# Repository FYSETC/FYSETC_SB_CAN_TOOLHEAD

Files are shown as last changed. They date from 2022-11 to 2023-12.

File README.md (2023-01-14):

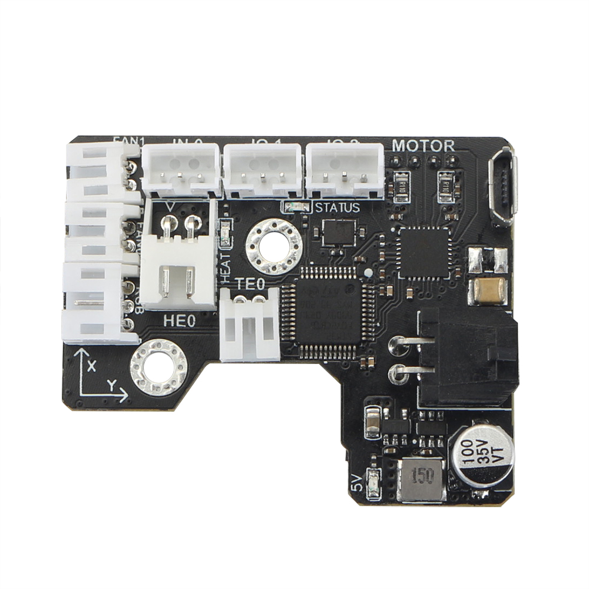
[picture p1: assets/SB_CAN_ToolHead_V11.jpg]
SB_CAN_ToolHead


# Introduction

The SB CAN Tool Board is a highly integrated printhead control board. Based on STM32F072, running Klipper firmware. Onboard TMC2209 stepper motor driver, AXL345 acceleration sensor, and other necessary interfaces. And comes with a 2.5m 4-core cable for easy out-of-the-box use.

# Feature

- Based on STM32F072
- Onboard 1M CAN transceiver
- Onboard TMC2209
- 2x 0.5A MAX PWM interface for controllable fan (default VIN power supply, 5V optional)
- 1x signal input interface (VIN power supply, with level conversion)
- 2x signal input and output interface (5V power supply, with pull-up resistor)
- 1X 5V single wire RGB interface (1A MAX)
- 1x 4A MAX PWM output for heating rod
- 1x ADC interface for heating rod temperature acquisition
- MX3.0 2X2 interface for power and CAN signal access
- 1x Micro USB for firmware uploading
- Comes with 2.5m 4-core cable, 2x16AWG+2x24AWG
- Comes with terminal housing and wire crimping tabs

# Where to Buy

Taobao

Aliexpress

Official website

# Docs

Check our wiki: [SB CAN TH - FYSETC WIKI](https://wiki.fysetc.com/SB%20CAN%20ToolHead/)

# Contact US

QQ group：1041794121

Facebook group：https://www.facebook.com/groups/197476557529090

Discord：https://discord.gg/Fb6FdND4

email：support@fysetc.com

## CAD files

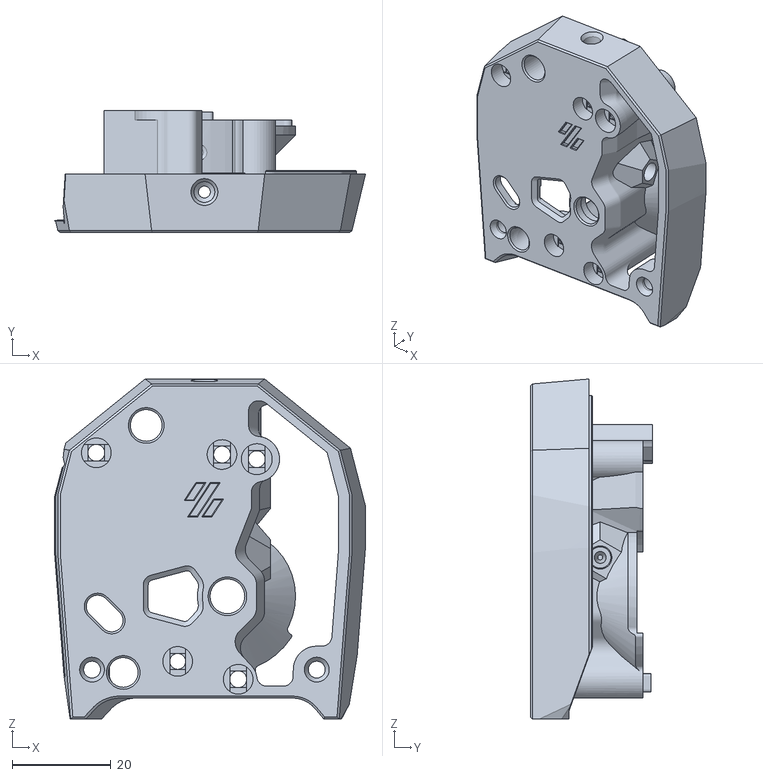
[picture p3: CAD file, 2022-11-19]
STLs/main_body^Clockwork2(2)_Clockwork2.STL
62.8 x 24.7 x 68.7

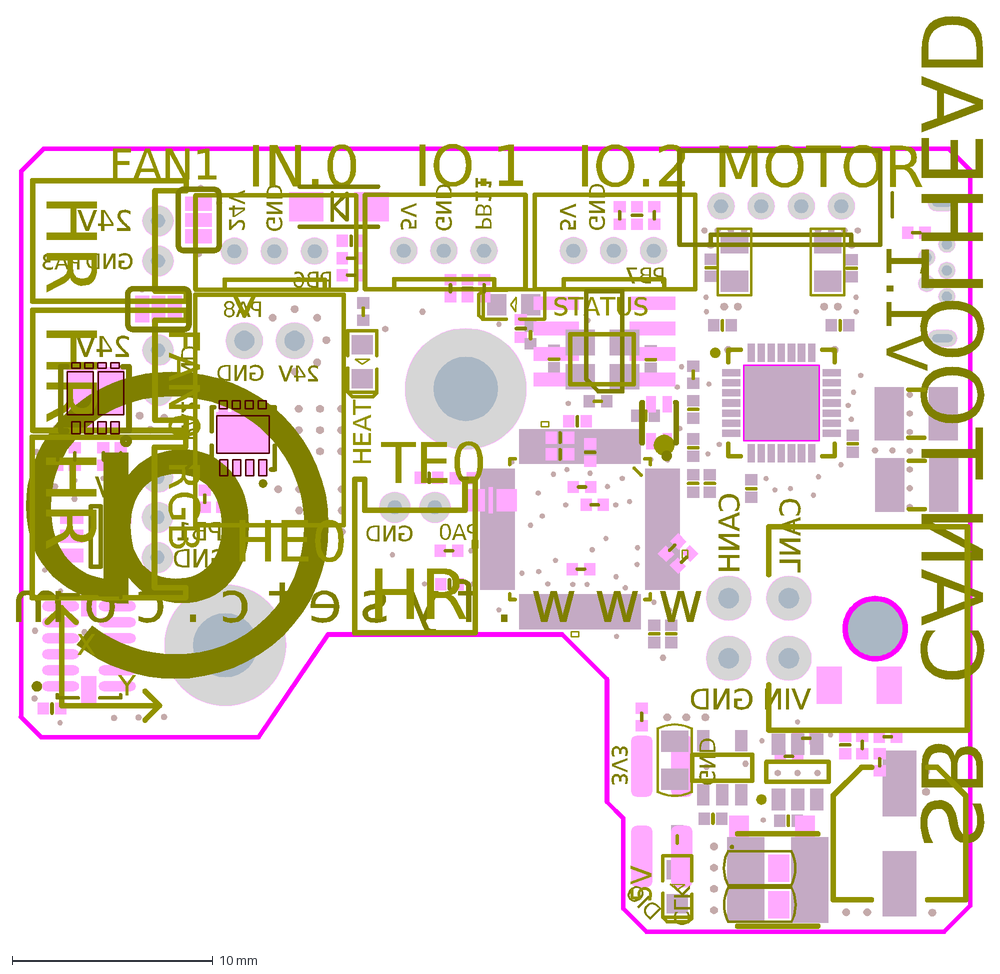
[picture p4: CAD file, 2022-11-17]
SB CAN TOOLHEAD V1.1.DXF
PA8
GND
V1.1
PB6
PA2
@
5V
24V
PB11
CANL
PB7
3V3
w w w . f y s e t c . c o m
PA3
PA0
PB1
CANH
DIO
VIN
SB CAN TOOLHEAD
CLK
IO.2
HE0
IN.0
FAN1
TE0
IO.1
FAN0
RGB
MOTOR
X
Y
STATUS
HEAT
HR

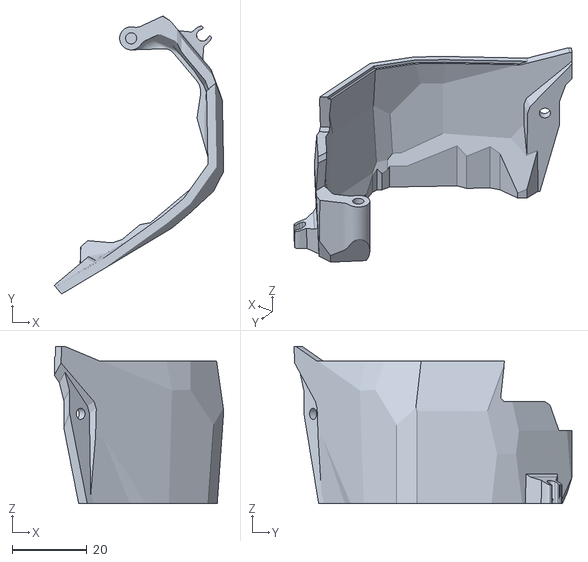
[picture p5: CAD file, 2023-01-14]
STLs/Clockwork2-adjusted.STL
45.4 x 74.5 x 42.2

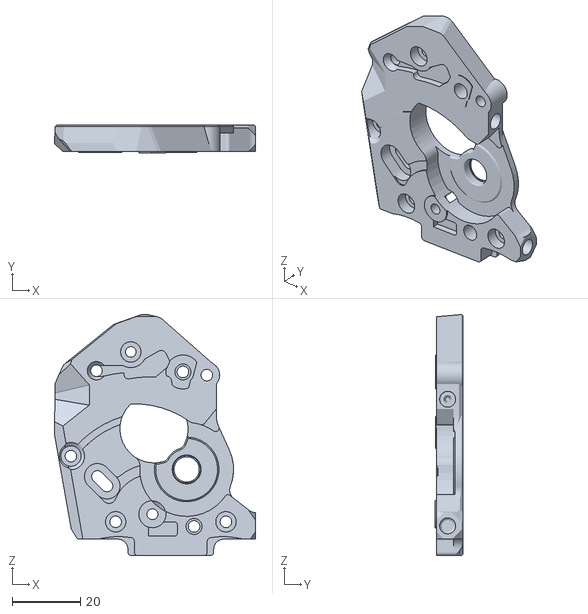
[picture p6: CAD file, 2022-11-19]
STLs/motor_plate^Clockwork2(2)_Clockwork2.STL
59.1 x 8.20 x 70.8

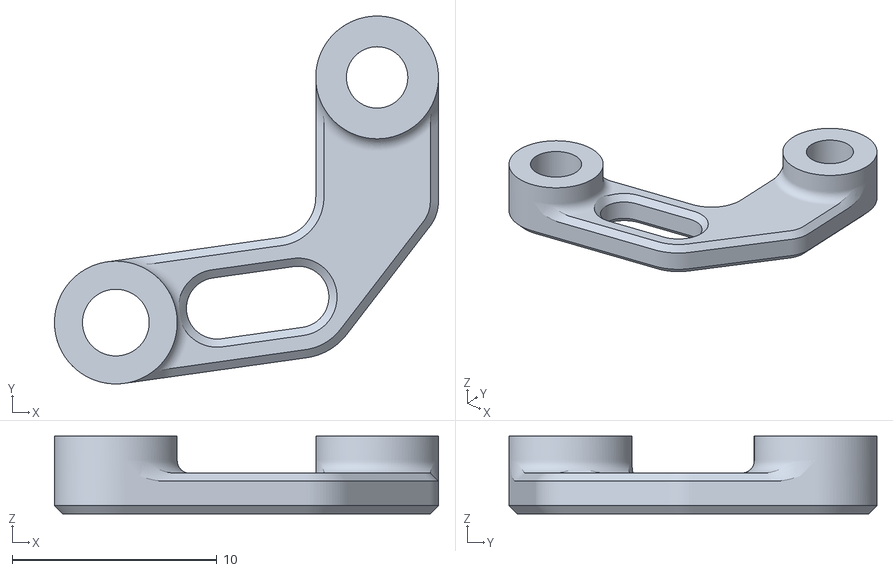
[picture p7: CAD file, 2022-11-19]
STLs/pcb_spacer.STL
18.8 x 18.0 x 3.80

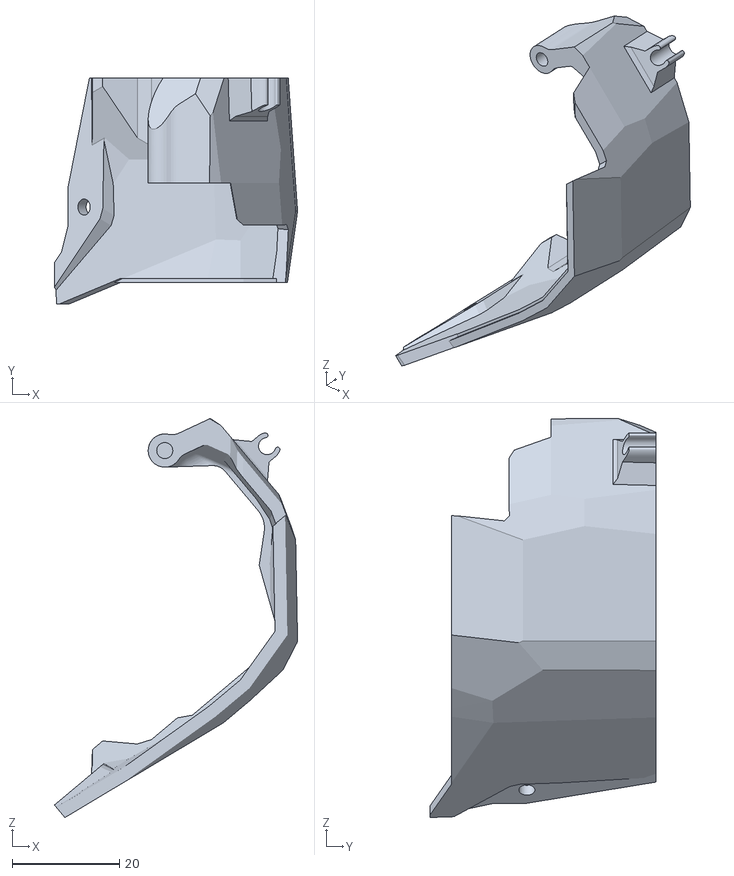
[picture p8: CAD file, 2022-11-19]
STLs/Clockwork2.STL
45.4 x 42.2 x 74.5

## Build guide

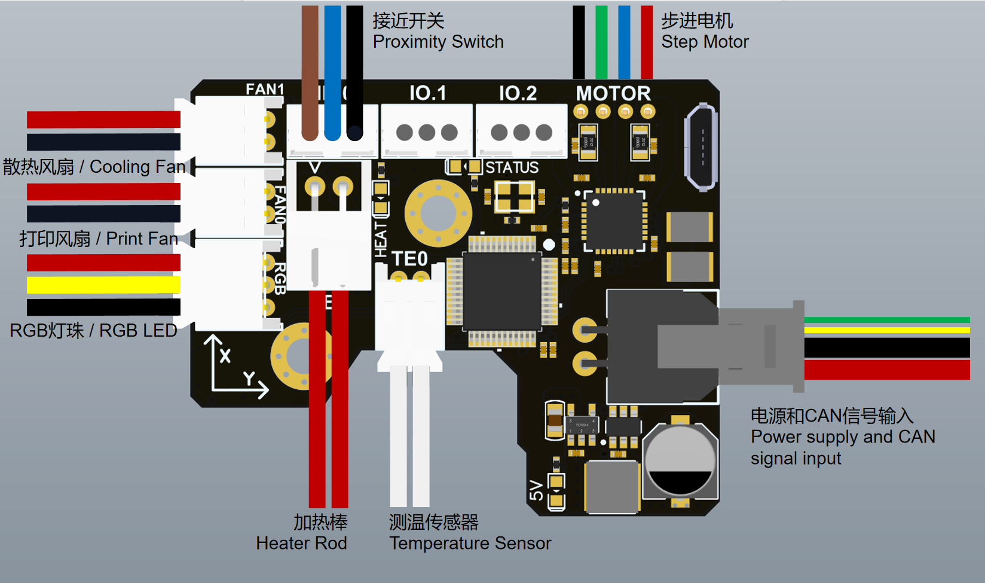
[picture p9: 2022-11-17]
assets/SB CAN ToolHead_Wiring.png

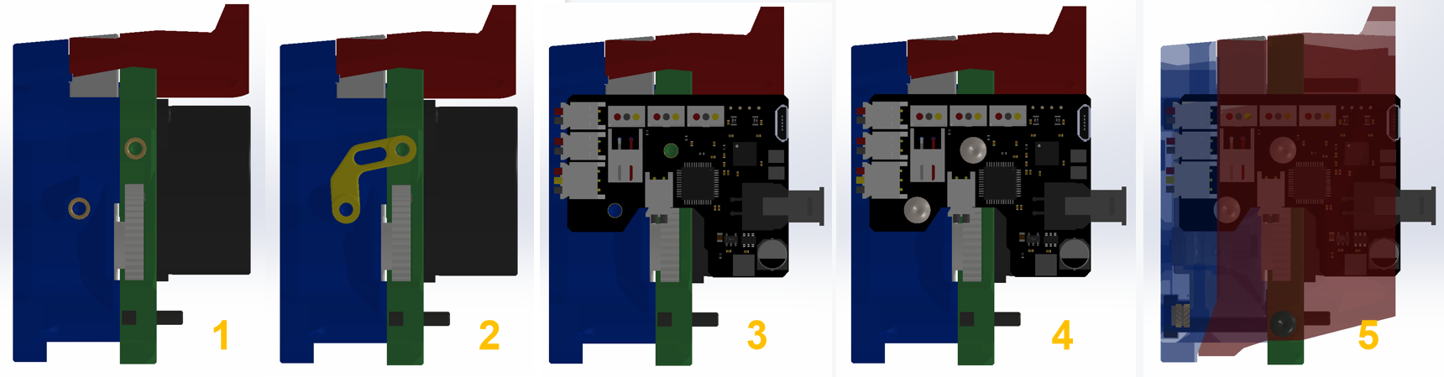
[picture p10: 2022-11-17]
assets/SB CAN ToolHead_Install.png

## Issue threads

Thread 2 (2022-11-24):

蜘蛛主板can收发器,配合sb_can_toolhead的使用方法

git-czy, 2022-11-24:
menuconfig：
蜘蛛主板menuconfig
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
sb_can_toolhead menuconfig
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
问题：
1.使用`~/klippy-env/bin/python ~/klipper/scripts/canbus_query.py can0`命令只能查询到主板的uuid,无法获取sb_can_toolhead的uuid。已经困扰几天了
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
取下收发器也只有一个uuid，是因为收发器没有正常工作？
2.wiki上的https://wiki.fysetc.com/SB%20CAN%20ToolHead/，menuconfig配置的STM32F103，sb_can_toolhead使用的STM32F072芯片，是不是不太对

求蜘蛛主板can收发器,配合sb_can_toolhead的正确配置方法

git-czy, 2022-11-24:
正确的配置方法，蜘蛛主板menucofnig见问题中图，sb_can_toolhead menuconfig如下图
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

最终效果如下
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
有两个uuid,取下can板再执行一次命令，即主板uuid

GerogeFu, 2022-12-03:
蜘蛛主板如果不需要加入到 CAN BUS 网络中，就采用 USB 或者 串口的配置进行连接即可，如果用 CAN 收发器的将蜘蛛主板加入到 CANBUS 网络的话，按以下配置
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
你可以先不管蜘蛛主板的，先把 SBCAN 的 CAN 调通，然后再来调试蜘蛛板的 CAN

git-czy, 2022-12-03:
> 蜘蛛主板如果不需要加入到 CAN BUS 网络中，就采用 USB 或者 串口的配置进行连接即可，如果用 CAN 收发器的将蜘蛛主板加入到 CANBUS 网络的话，按以下配置 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 你可以先不管蜘蛛主板的，先把 SBCAN 的 CAN 调通，然后再来调试蜘蛛板的 CAN
>
> SBCAN 正确的接线应该是 树莓派 -> UCAN模块 -> CANBUS -> SBCAN 模块

谢谢，我按照这种方法，已经解决了，目前正常使用

Closed 2022-12-03.

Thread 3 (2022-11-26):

Differences between STLs in this repository and the official stealthburner repo

geoffdavis, 2022-11-26:
Other than the "hook" on the top of `Clockwork2.STL`, I can't find any differences in the shape of the objects in this repository and the office Voron STLs.

Am I missing something, or is it just a matter of old STLs from the beta version of the Stealthburner?

23Jacky, 2022-12-13:
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
Cutting is done here

numindast, 2023-01-09:
It would be good to know if the "main body" and "motor plate" STLs are any different from the Stealthburner stock parts.

I'm also curious as I would like to print an ERCF main body myself to get the ECAS fitting on top, but want the SB CAN PCB to work as intended too. Thanks!

Interfredzo, 2023-11-29:
I've noticed that most changes are due to old beta data used.
Also the board colides with the spacer (the official and the one provided by fysetc).
I've compared the original release date of the motorplate from the voron team (green transolcent) with the one from fysetc. The diferences are not realted to the PCB at all. ->Use the official voron repo data and mirror the space
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
r.
![collisionSpacer](https://github.com/FYSETC/FYSETC_SB_C
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
AN_TOOLHEAD/assets/123958845/8ac8dbe7-e5ee-48a0-acaf-e47c895c8559)

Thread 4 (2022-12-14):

Does this toolhead PCB require the CAN bus expander?

OzzieOrca, 2022-12-14:
I've got a Spider V1.1 board and am looking at purchasing this toolhead PCB from https://www.fysetc.com/products/fysetc-sb-can-tool-board-based-on-stm32f072-support-klipper-with-tmc2209-axl345-acceleration-sensor-for-3d-printer-parts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.

Is this CAN bus expander required?
https://www.fysetc.com/products/fysetc-canbus-expander-module-for-spider-board?variant=42187841994927

In this repo/wiki you've got a bunch of pinouts for the toolhead PCB but not how to connect it to the Spider. https://github.com/FYSETC/FYSETC-SPIDER#can-bus shows using it but for connecting to the Raspberry Pi. I assume it's needed to go from UART to CAN bus? Does the CAN bus expander GND need to be tied to ground?

I'm going to be using the Stealthburner Rapido toolhead and probably leave the Clockwork 1 in place. Looks like the Clockwork 1 might be missing a mounting screw hole? I'll figure something out.

Anything else I should know as far as compatibility? Will I be ok with the V1.1 Spider board?

Either way, updating the docs to mention whether it's required and how to connect would be great :) I could make a PR if needed.

Thanks!

numindast, 2023-01-09:
The Spider CAN expander is not required, unless your intention is to operate the Spider via CAN from the Klipper host. My understanding is this is not necessary and not always desirable.

I've got the expander also and it's just going to sit in a box. In my case, I use UART from the Raspberry Pi to the Spider (rather than USB, but either is perfectly acceptable). Add the UCAN to a USB port on your Pi and the other end of the UCAN is the CAN bus to the toolhead. Just wired this up today and it works.

Hope this helps

MdShahrilOGP, 2023-04-09:
Hello @numindast, I sincerely apologise for tagging you directly, but I am attempting to set up the SB CAN TH but am failing rather miserably. I am on a spider v2.2, and the connection goes like this RPI > UCAN > SB CAN TH. I followed the FYSETC's guide [here](https://wiki.fysetc.com/SB%20CAN%20ToolHead/) but I still can't get hte canbus_uuid at all. I've inserted the can0 config into /etc/network/interfaces.d directory too, but nothing works.

May I please ask the steps you took to get yours working? Thanks in advance sir!

numindast, 2023-04-10:
Hi - what are you seeing when trying to run the `canbus_query.py` script? Nothing at all (eg. returns to shell prompt) or a bunch of errors?

Here's the process I followed. I'm probably overexplaining but hopefully if you missed a step you can catch it, or else this could be useful for someone else.

First connecting USB to the RPi from the UCAN. You should be able to `lsusb` and be able to see the following USB device in the output:
`Bus 001 Device 003: ID 1d50:606f OpenMoko, Inc. Geschwister Schneider CAN adapter`

If not, try a different USB cable perhaps, or a different USB port on the RPi. The UCAN came out of the box with the "candleLight" firmware so I did not have to flash the UCAN firmware myself. You won't be able to make progress until that entry is shown above in your `lsusb`.

You can confirm if your RPi likes the can0 setup by checking with `ifconfig` and view the output:

`can0: flags=193<UP,**RUNNING**,NOARP>  mtu 16
        unspec 00-00-00-00-00-00-00-00-00-00-00-00-00-00-00-00  txqueuelen 128  (UNSPEC)
        RX packets 14816  bytes 111412 (108.8 KiB)
        RX errors 0  dropped 0  overruns 0  frame 0
        TX packets 1164  bytes 6843 (6.6 KiB)
        TX errors 0  dropped 0 overruns 0  carrier 0  collisions 0`

"Running" is what you want to see here. If it's not running, try `sudo ip link set can0 up type can bitrate 500000` (shamelessly stolen from the Voron discord #voron_electronics pinned posts). If that fails, ask in Discord for help, because I don't know.

Next up, connect your toolhead cable (you don't even need to install the PCB to start talking to it). The 4-pin Molex goes on the PCB of course, and the other end - CAN H/L to the appropriate screw terminals, and GND to a V- on your 24v power supply. That's also going to be where the CAN cable's power wires go, V+ and V- as well. You may already have done this, just confirming though. GND or V- need to be connected from both UCAN and the CAN cable to the toolhead.

Also, the 24v power must be turned on to power the toolhead PCB, it will not light up from just the CAN H/L wires. You'll know it's powered up when a red LED goes on near the bottom of the board.

If you haven't yet, here is when you can flash Klipper to the toolhead's MCU. Link to [Fysetc's Wiki on that here](https://wiki.fysetc.com/SB%20CAN%20ToolHead/#3-firmware-guide).

Be sure to follow their steps carefully. It's worth the extra effort.

The [RPi should be able to see/report](https://www.klipper3d.org/CANBUS.html#finding-the-canbus_uuid-for-new-micro-controllers) an uninitialized STM32 on the bus. Snag that canbus_uuid, stick it in your printer.cfg (I named mine `[mcu toolhead]`) and go forth.

Good luck - report back!

Kravenovic, 2023-04-10:
Hello @numindast, thank you so much for taking the time to reply me! Running this command `~/klippy-env/bin/python ~/klipper/scripts/canbus_query.py can0` returns this output:

```
Traceback (most recent call last):
  File "/home/pi/klipper/scripts/canbus_query.py", line 64, in <module>
    main()
  File "/home/pi/klipper/scripts/canbus_query.py", line 61, in main
    query_unassigned(canbus_iface)
  File "/home/pi/klipper/scripts/canbus_query.py", line 21, in query_unassigned
    bustype='socketcan')
  File "/home/pi/klippy-env/lib/python3.7/site-packages/can/interface.py", line 127, in __new__
    return cls(channel, *args, **kwargs)
  File "/home/pi/klippy-env/lib/python3.7/site-packages/can/interfaces/socketcan/socketcan.py", line 594, in __init__
    bind_socket(self.socket, channel)
  File "/home/pi/klippy-env/lib/python3.7/site-packages/can/interfaces/socketcan/socketcan.py", line 459, in bind_socket
    sock.bind((channel,))
OSError: [Errno 19] No such device
```

When I use `lsusb` I get this:

```
pi@mainsailos:~/klipper $ lsusb
Bus 002 Device 001: ID 1d6b:0003 Linux Foundation 3.0 root hub
Bus 001 Device 005: ID 1d50:614e OpenMoko, Inc.
Bus 001 Device 002: ID 2109:3431 VIA Labs, Inc. Hub
Bus 001 Device 001: ID 1d6b:0002 Linux Foundation 2.0 root hub
```

I don't see the `OpenMoko, Inc. Geschwister Schneider CAN adapter`.
Based on all the information I received from you, it seems that the problem lies with the fact that I still do not have a can0 interface which is up; despite me configuring the can0 file in /etc/network/interfaces.d

Once again, thank you so much for replying and for the assistance! Hope I can get this working soon!

numindast, 2023-04-10:
Hello - the OpenMoko is probably the UCAN. Unplug it and do another `lsusb` to see if that entry disappears. I'm not sure what it means that the OpenMoko USB descriptor in the output is different. I had the bad fortune not to have any issues so I'm not in a position to have a good idea.
If you aren't already on the Voron discord, definitely ask there in the #voron_electronics sub. There are a lot of people there with more experience (and brains!) than me!

I can think of one question: what OS are you operating on your RPi? Is it Raspberry Pi OS? Debian Buster or Debian Bullseye (newer)? I wonder if your Pi really is ready for can0. I don't recall installing anything but I'm using a new Bullseye install from the Pi foundation, and used Kiauh to set up all the "stuff" for me for Klipper (etc).

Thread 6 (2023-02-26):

Will this board handle a Rapido hotend?

RZ3D, 2023-02-26:
Will this board handle a Rapido hotend or is the draw too high?

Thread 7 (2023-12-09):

FYSETC Vorn SB CAN Toolhead V1.3

solrac8874, 2023-12-09:
Where can I find installation, schematics, etc. V1.3 version of this tool head?  I tried installing it using the Fystec SB CAN Toolhead Wiki (https://wiki.fysetc.com/SB%20CAN%20ToolHead/#31-menuconfig).  But when following trying to do 3.2 Firmware Upload step 4: Plug in SB-CAN-TH board 24v socket to power on it( Get the power from machine PSU); the Vin Fuse popped.  Now the board no longer powers on.

The wiki page and github site for the Fystec SB CAN Tool Head is only for V1.1 of the board and have not be updated for V1.3.  Seems like my board was fried from following the V1.1 Wiki Instructions.

Interfredzo, 2023-12-11:
Can confirm this!!!!!

Following all steps destroys the board after flashing!!!

eliwong, 2023-12-13:
We already updated the wiki. Please check!

solrac8874, 2023-12-13:
Thanks. I wish the wiki and github were updated several months ago before I bought the CAN Toolhead board in September 2023 or when V1.3 was released.

The wiki & github should have or include pictures of the V1.3 board front & back.  Also maybe helpful to highlight the differences between V1.1 & V1.3 board (e.g. different specs, components, etc.) like the Amazon product page describes.

Is the Vin Fuse (F1 - 5A) part shown on the V1.3 schematic/position diagrams the same as the Vin Fuse (F1 - ASMD1206-300) part shown on the V1.1 schematic/position diagrams?  The V1.3 schematic doesn't show the fuse part number like the V1.1 schematic. Are there any other components besides the fuse that are different and potentially at risk of being damaged by following the original V1.1 instructions?

I'm hoping I can just replace the Vin Fuse and get the V1.3 board working again so I can try to follow the new V1.3 instructions and confirm the new updates work.

Interfredzo, 2023-12-13:
The TMC2209 might be damaged.

I've also noticed that JP3 and R18 are actually missing on the board:

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

solrac8874, 2023-12-15:
R18 and JP3 are missing from my board too...  hope that's not a mistake.  Seems R18 and JP3 trace to CANL and CANH.
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

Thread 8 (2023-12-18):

CAN 120 Ohm terminating resistor missing on V1.3

Interfredzo, 2023-12-18:
The 120 ohm terminating resistor is missing on the actual PCB.

See JP3 and R18 on the shematics.

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

Also seems to be the case in the official product shots:

[https://ae01.alicdn.com/kf/S26268b260ddb4098bd3d542a5e0a9499Z.jpg](url)

Gagag1998, 2023-12-19:
Hello, dear friend, it seems that your motherboard is version V1.1, which is not available in this version. It is only available in version V1.3.
https://www.aliexpress.us/item/3256804693763411.html?

thisiscam, 2024-01-14:
I can verify this on my board. The CANH and CANL are completely disconnected with no termination resistors in between. This board doesn't seem to function correctly either --- I get consistent MCU timeouts on this board.

Interfredzo, 2024-01-29:
This is also the case on v1.3b. Soldering pads are present now compared to V1.3 but the resistor is missing. (Labeling for both boards is v1.3 though). I got a replacement board from FYSETC after the fuse and tmc driver blew up because i followed the manual ...

I soldered a 120ohm 0805 resistor to R18 now it's working.

To bad FYSETC is sending out boards which couldn't function in first place (resitors missing or not even planed). Or which blow up because the docu is not updated.

At least the customer support was fast in sending a replacement. And the wiki is updated now.
Would be nice if FYSETC will update their wiki so that everyone knows there needs to be a 120R if you use this as CAN end node (which is the default case for most users)

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

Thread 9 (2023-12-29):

Fan tachometer?

thisiscam, 2023-12-29:
Is the "fan0 tach" pin in the schematics actually connected to anything?

Interfredzo, 2024-01-29:
No. I also have a tach for the hotend. which I would highly recommend: https://ellis3dp.com/Print-Tuning-Guide/articles/useful_macros/hotend_fan_monitoring.html Had one fan failing and luckily I was near by.

You could use one of the IO connectors I guess. I will try it and leave a comment.

thisiscam, 2024-01-29:
I'm confused. If it's not connected to anything, how do you plan to use that pin? Are you suggesting soldering a wire onto the STM chip leg?

Interfredzo, 2024-01-29:
You can try soldering directly to the STM chip leg. I wouldn't recommend this unless your SMD soldering skills are very good. I would suggest using PB.6 PB.11 or PB.7 wich are on IN.O, IO.1 and , IO.2.. The tach signal connects the pull up to ground so the supply voltage of the van schould be irrelevant. So just connecting the ground and power of the fan to fan.0 or fan.1 and connecting the tachometer pin from the fan to the signal pin of IN.O, IO.1 and , IO.2 should work.

I guess the config should look like this. For Fan1 and signal to BP11 on IO.1
```
[fan_generic sb_can_fan1]
pin: sb_can_th:PA3
tachometer_pin: sb_can_th:^PB11
```

I didn't tried it yet and im no electronics engineer ;-) So no 100% guarantee.

Interfredzo, 2024-02-12:
OK I tested it with a Sunon 5V MF40100V1-1000U-G99 connected to IO.2: Power to 5V and Singal to PB7 to FAN1 only fround to PA.3

```
[fan_generic testfan]
pin: sb_can_th:PA3
tachometer_pin: sb_can_th:PB7
max_power: 1
cycle_time: 0.1
shutdown_speed: 0.0
kick_start_time: 0.5
off_below: 0.20
```
Since PB7 has a 10k pull-up already I didnt change it. Works flawless.

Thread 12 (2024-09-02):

Connector type for the power/CAN input on v1.3?

seanauff, 2024-09-02:
Does anyone know what connector this is? I would like to create a cable but can't find this connector anywhere

seanauff, 2024-09-03:
I managed to find it! It is an XT30(2+2). See [here](https://www.wellnowus.com/xt30pw22-male-gold-plated-plug-with-signal-pin-product/). Many options available on Aliexpress

Closed 2024-09-03.

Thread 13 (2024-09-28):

Step file of v1.3 corrupted?

5teveO, 2024-09-28:
I have downloaded the step file multiple times and opened in several different CAD packages.. none will open the file.

Are you able to replace the file with a working version?

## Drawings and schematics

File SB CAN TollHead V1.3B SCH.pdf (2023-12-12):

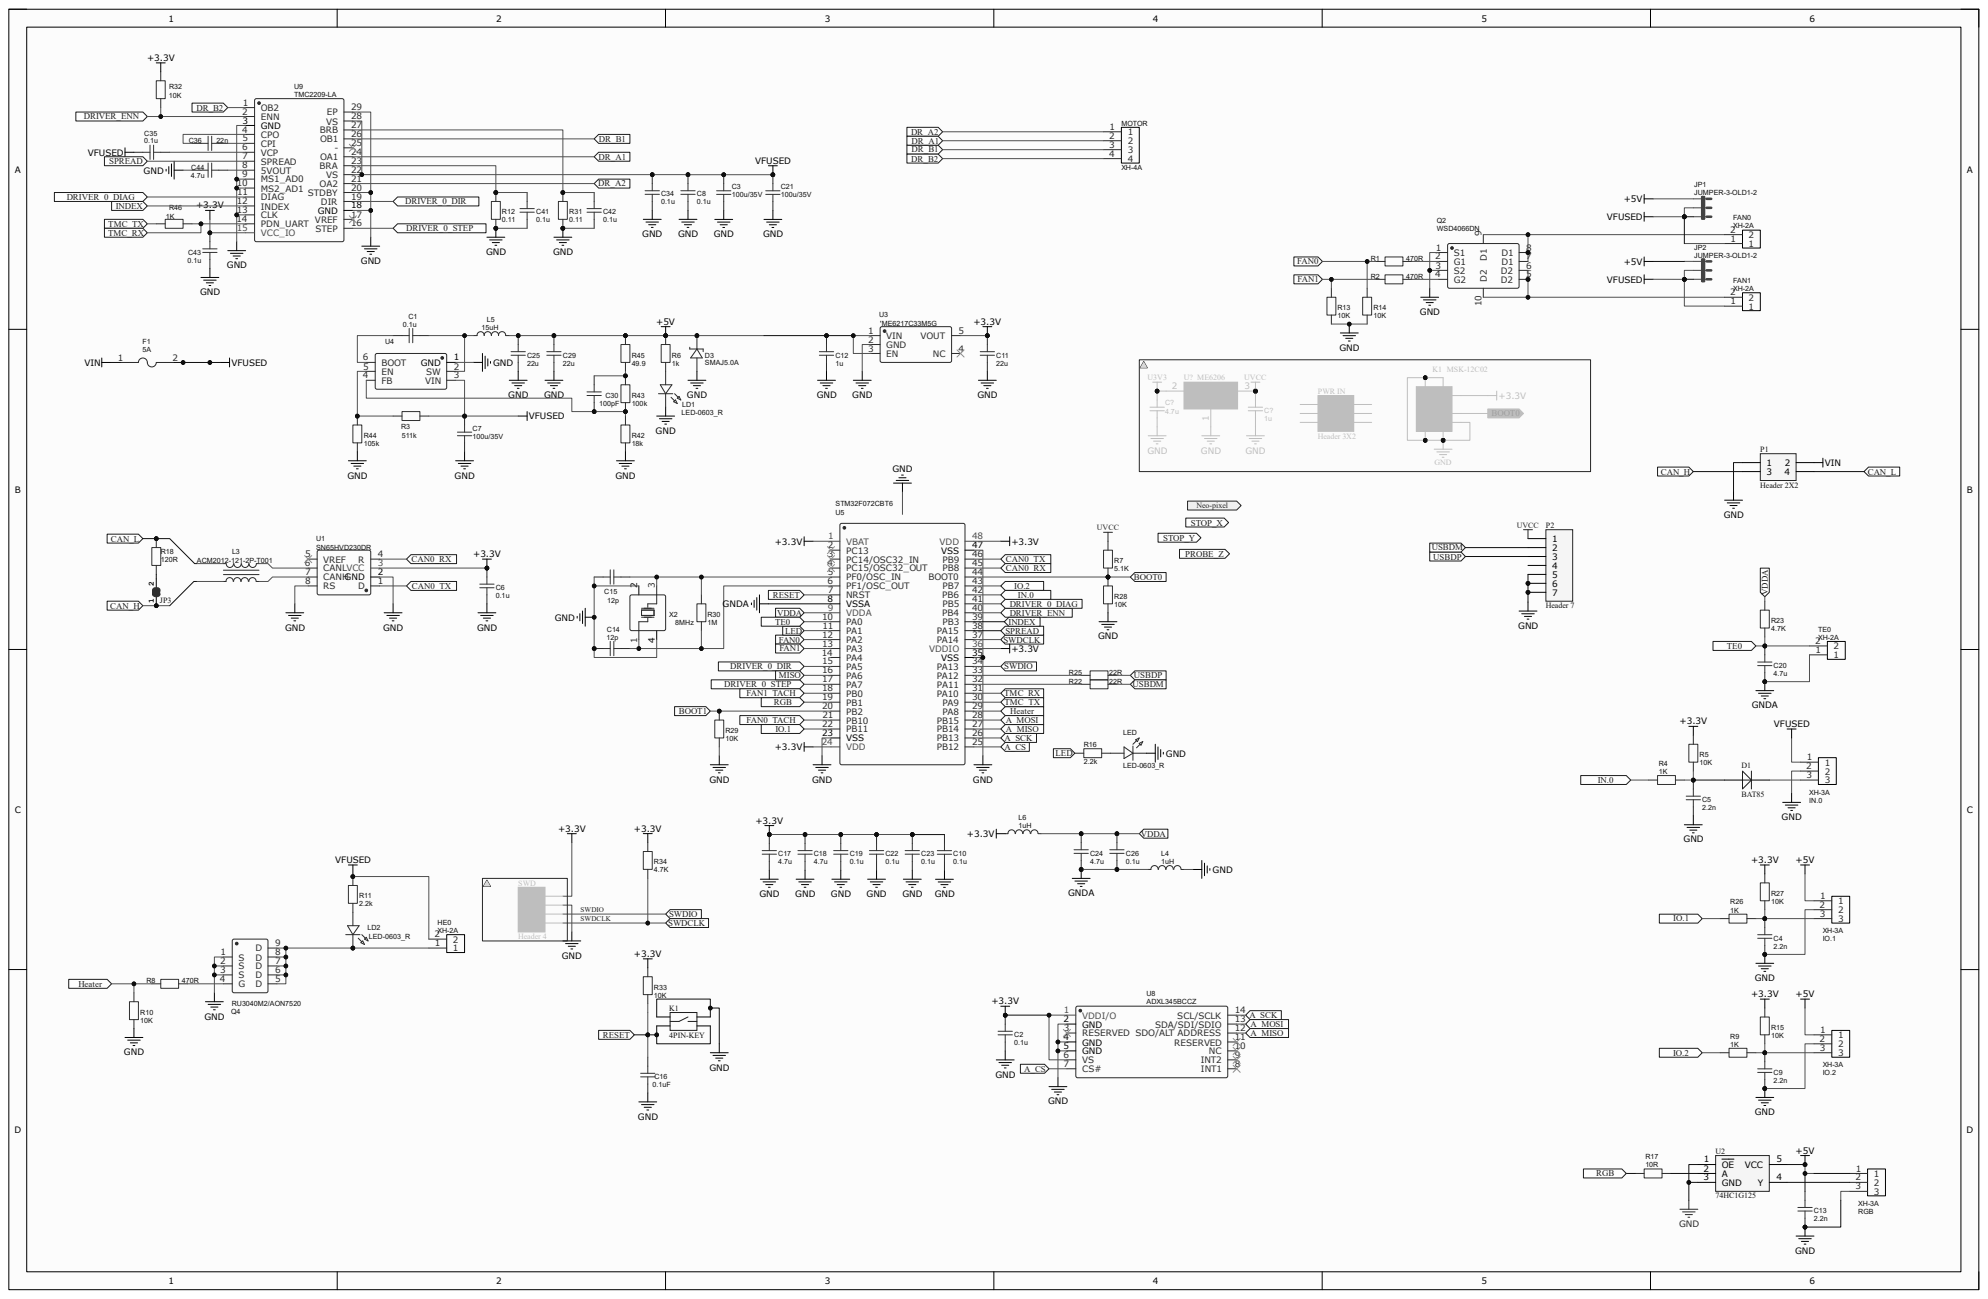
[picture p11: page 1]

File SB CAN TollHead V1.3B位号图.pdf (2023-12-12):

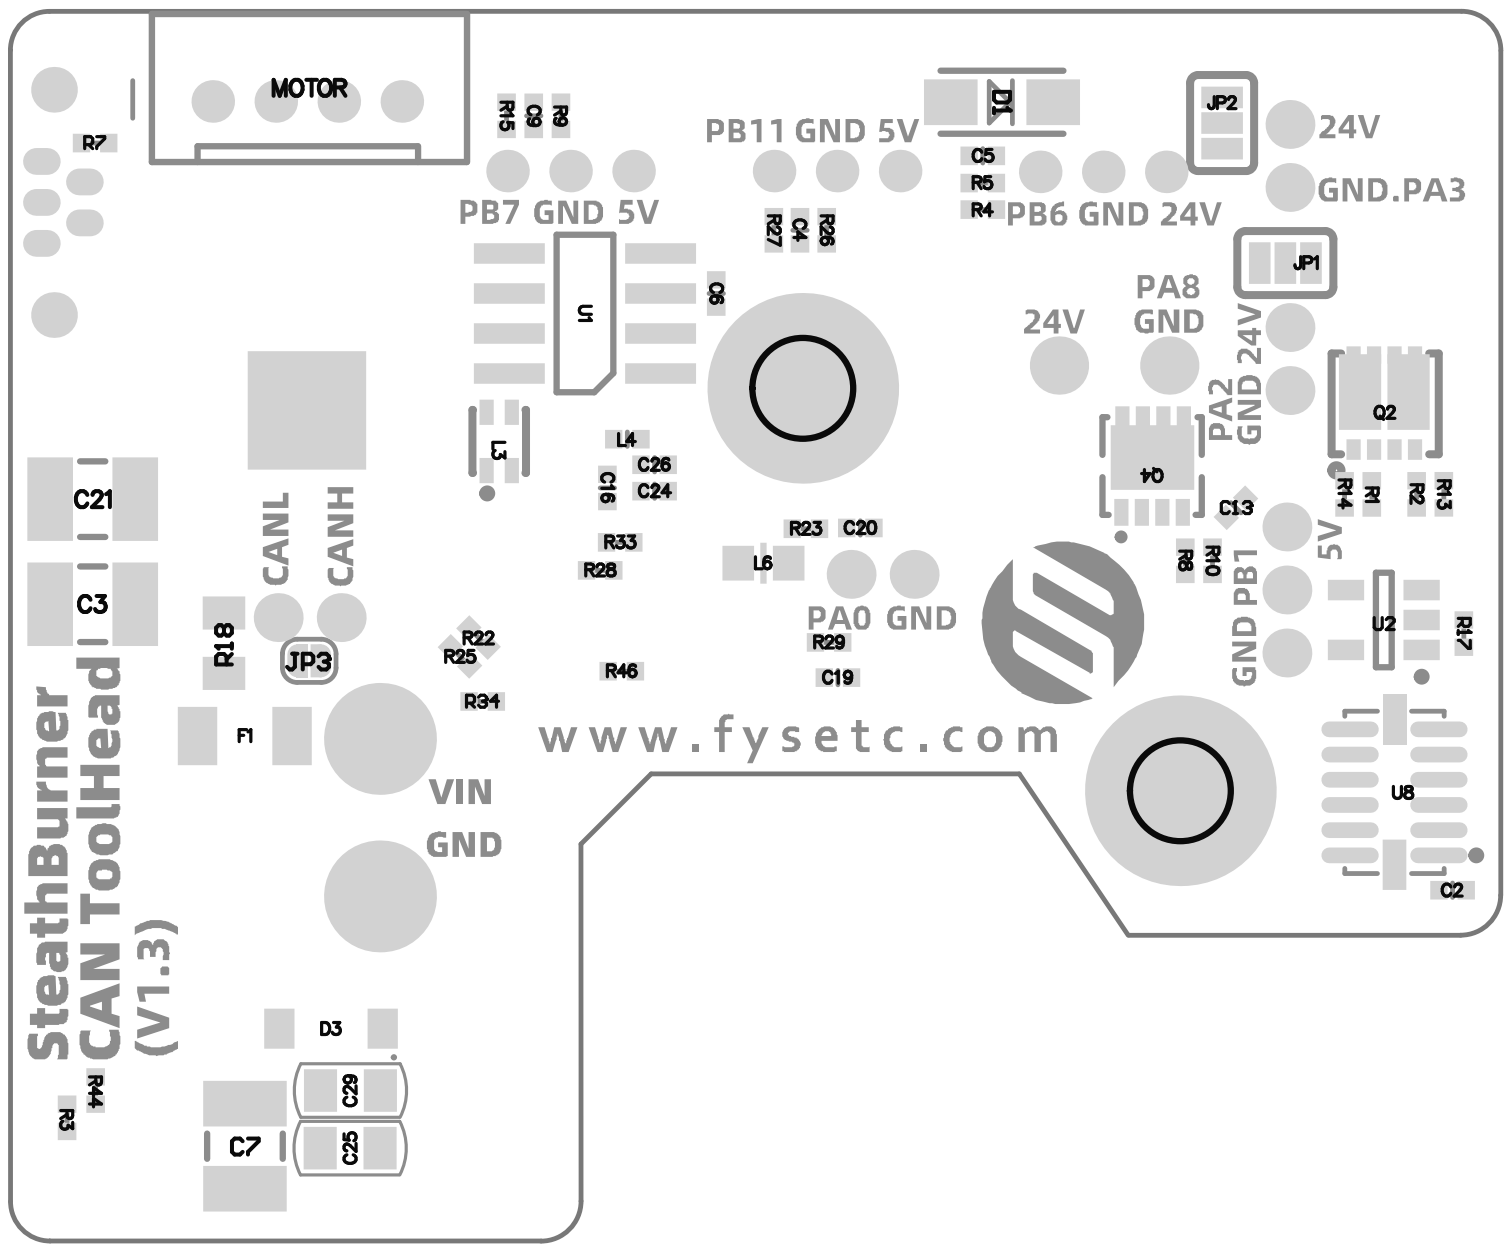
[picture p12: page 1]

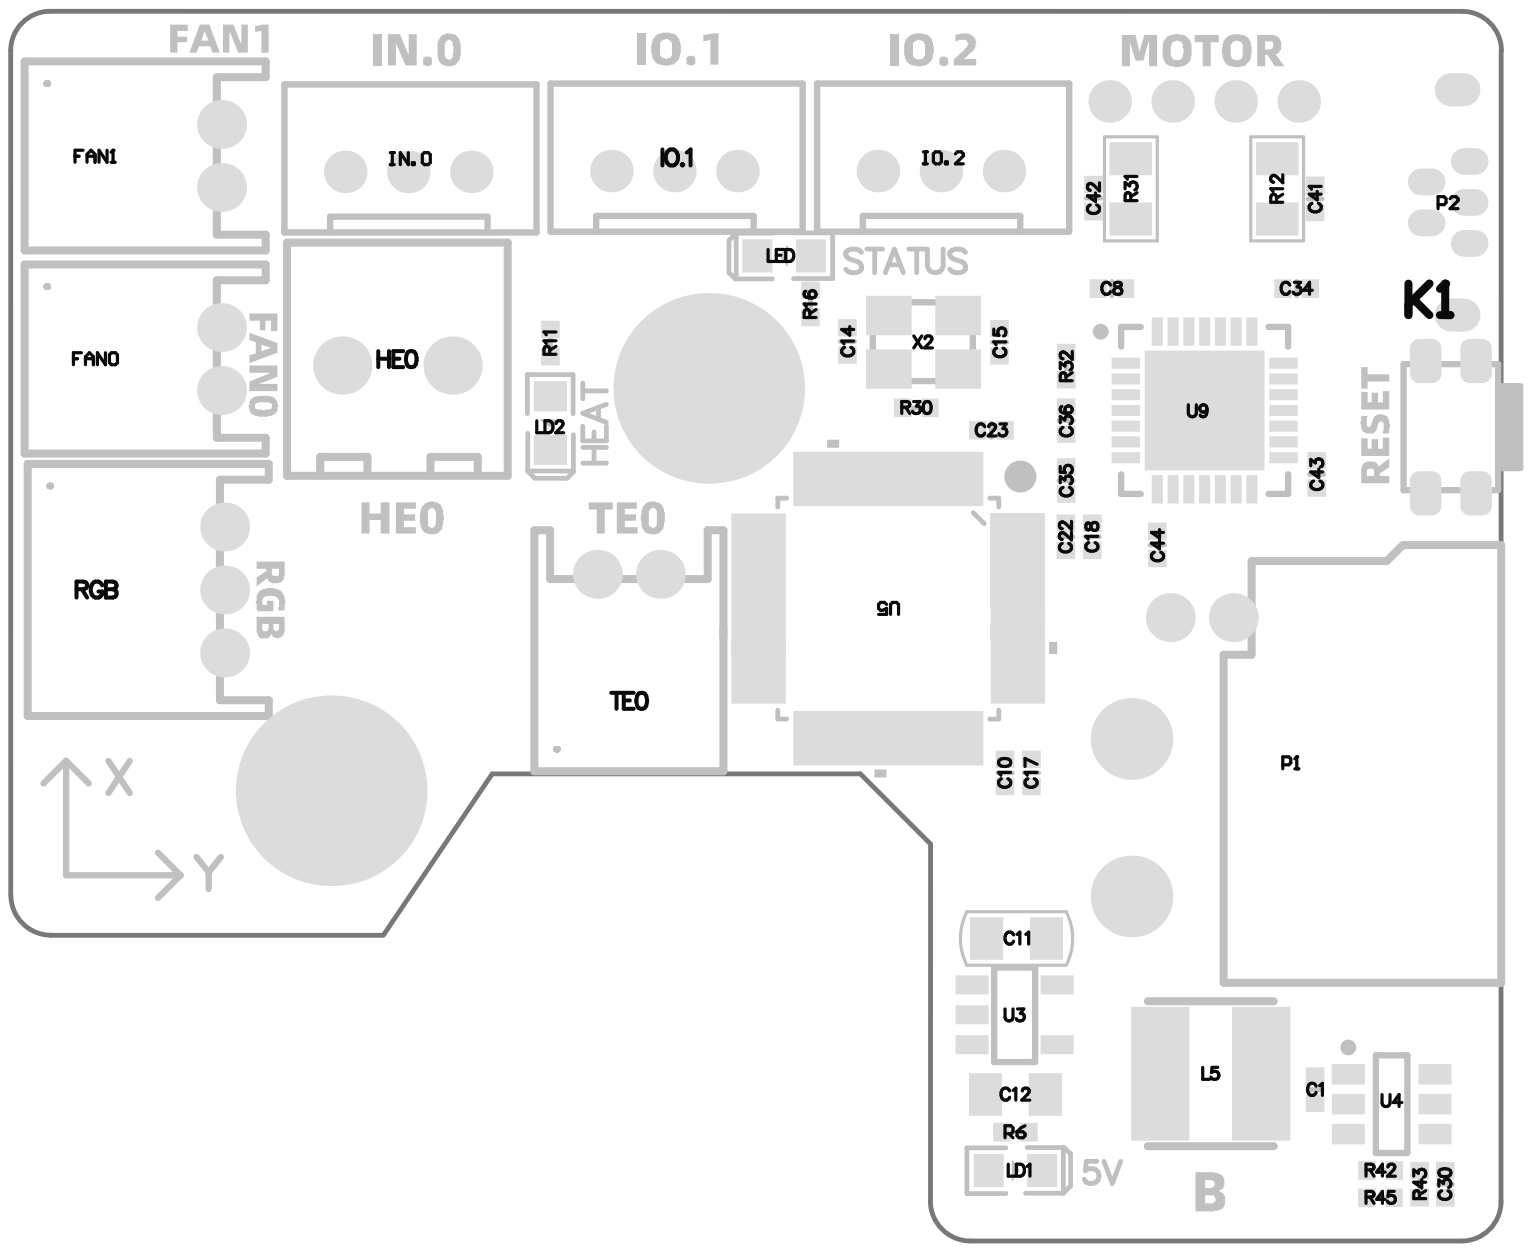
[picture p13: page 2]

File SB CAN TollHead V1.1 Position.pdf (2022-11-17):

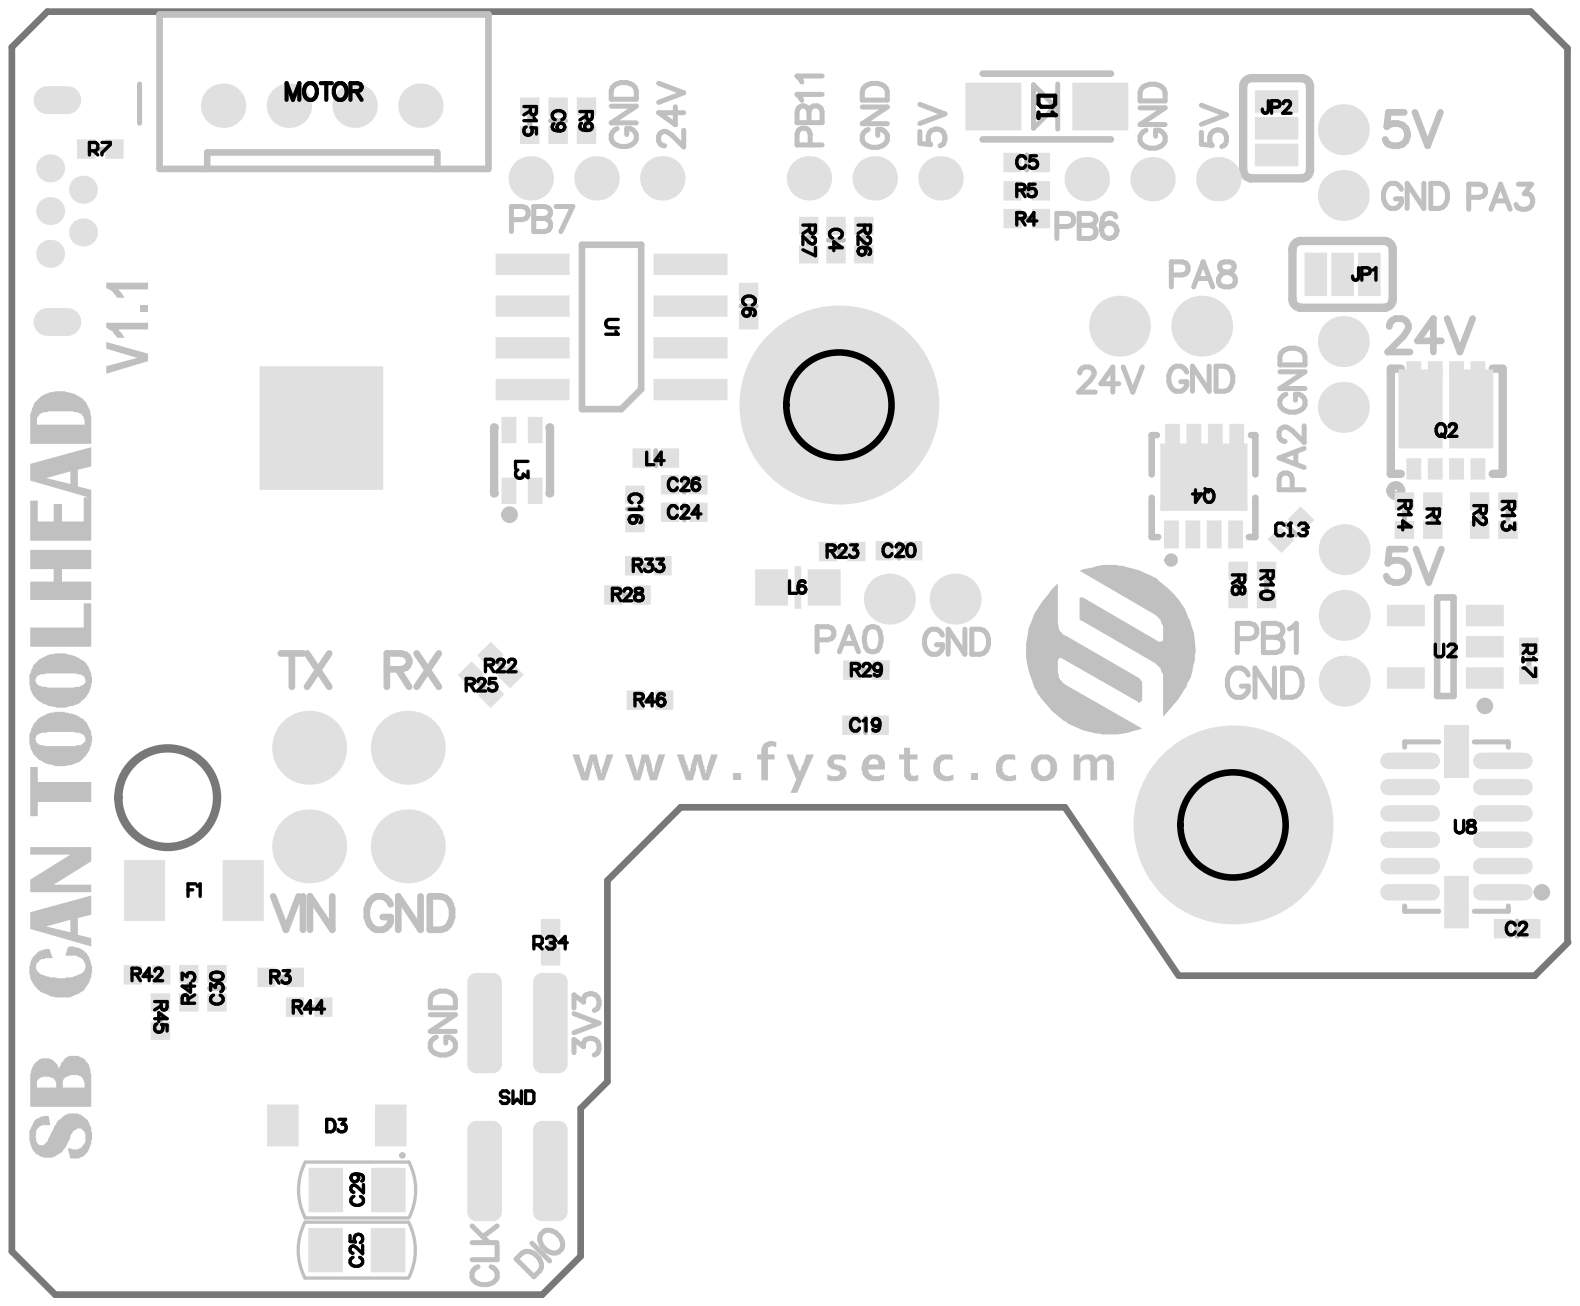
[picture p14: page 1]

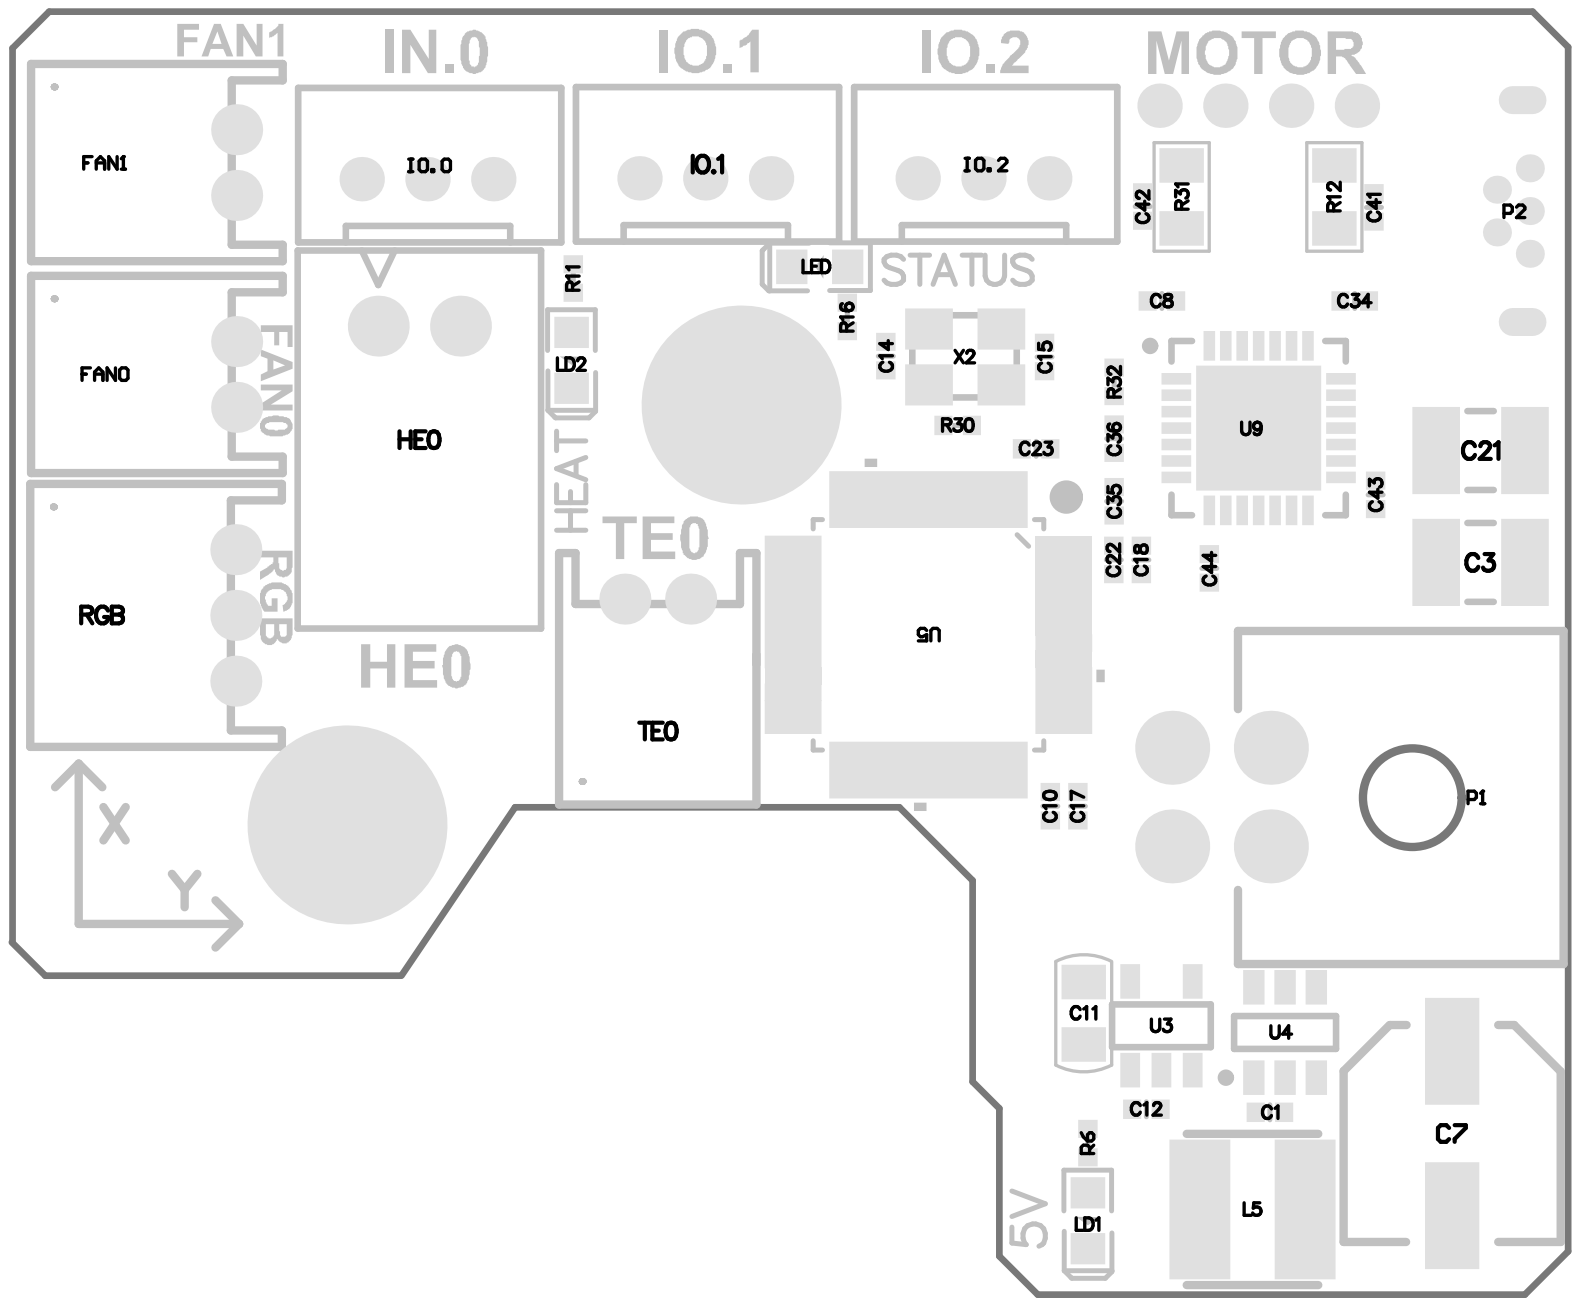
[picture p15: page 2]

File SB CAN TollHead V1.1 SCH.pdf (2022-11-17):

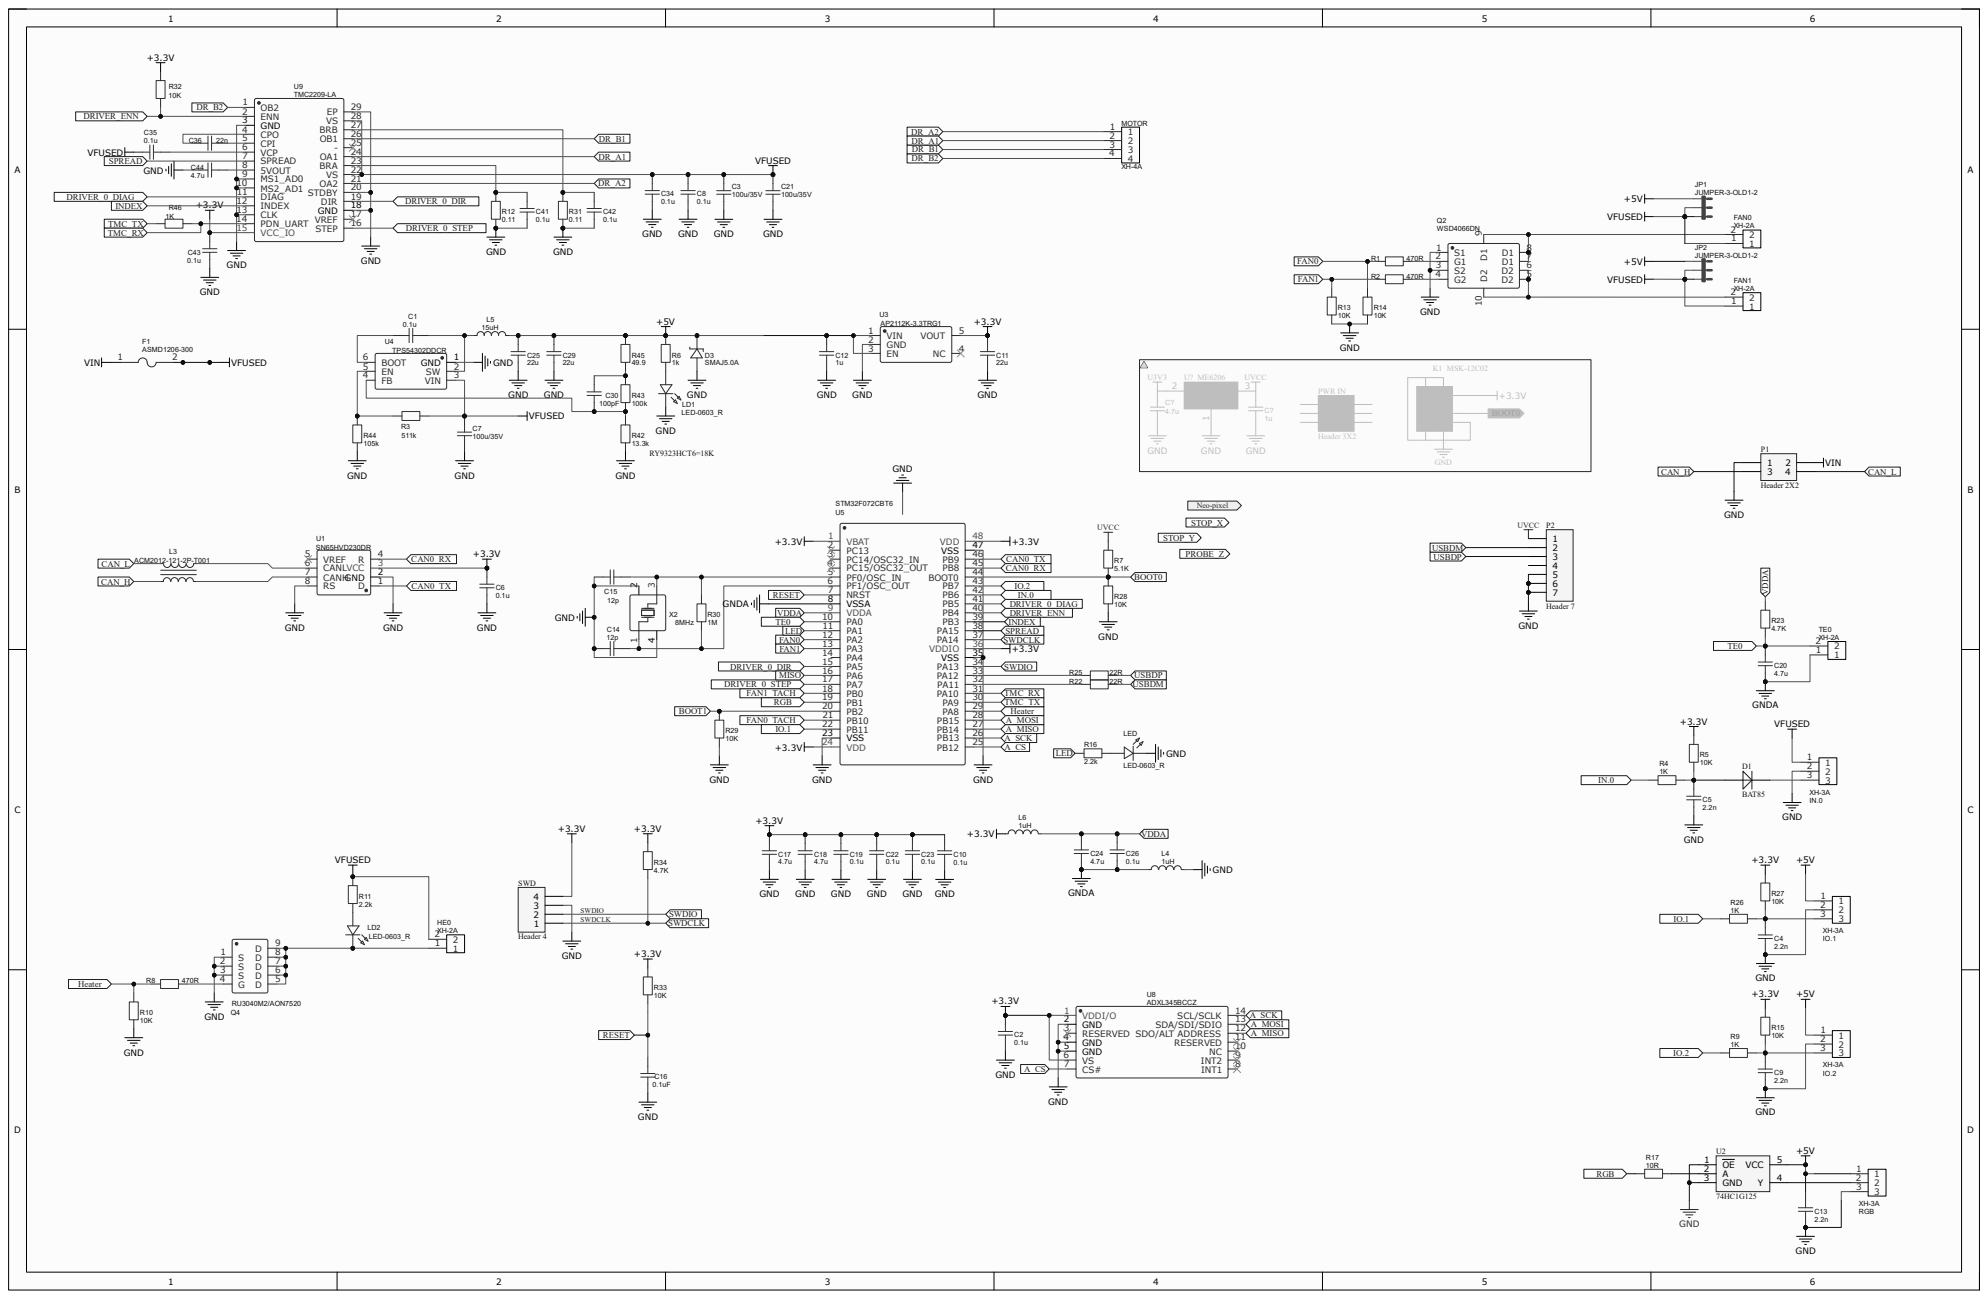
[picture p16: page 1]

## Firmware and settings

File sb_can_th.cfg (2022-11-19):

[mcu sb_can_th]
# Follow the instruction here https://www.klipper3d.org/CANBUS.html to get CAN id
canbus_uuid=e21f9e376be6

##  In E0-MOT Position
[extruder]
step_pin: sb_can_th:PA7
dir_pin: sb_can_th:PA5
enable_pin: !sb_can_th:PB4

##  Update value below when you perform extruder calibration
##  If you ask for 100mm of filament, but in reality it is 98mm:
##  rotation_distance = <previous_rotation_distance> * <actual_extrude_distance> / 100
##  22.6789511 is a good starting point for Bondtech 5mm gears
##  34.37086 for Bondtech 8mm gears (Galileo)
rotation_distance: 22.6789511   #Bondtech 5mm Drive Gears
##  Update Gear Ratio depending on your Extruder Type
##  Use 50:17 for Afterburner/Clockwork (BMG Gear Ratio)
##  Use 80:20 for M4, M3.1
##  Use 7.5:1 for Galileo
gear_ratio: 50:17               #BMG Gear Ratio
microsteps: 32
full_steps_per_rotation: 200    #200 for 1.8 degree, 400 for 0.9 degree
nozzle_diameter: 0.400
filament_diameter: 1.75
heater_pin: sb_can_th:PA8 # Heat
## Check what thermistor type you have. See https://www.klipper3d.org/Config_Reference.html#common-thermistors for common thermistor types.
## Use "Generic 3950" for NTC 100k 3950 thermistors
sensor_type: Generic 3950
sensor_pin: sb_can_th:PA0 # TH
min_temp: 10
max_temp: 270
max_power: 1.0
min_extrude_temp: 170
control = pid
pid_kp = 26.213
pid_ki = 1.304
pid_kd = 131.721
##  Try to keep pressure_advance below 1.0
#pressure_advance: 0.05
##  Default is 0.040, leave stock
#pressure_advance_smooth_time: 0.040

[tmc2209 extruder]
uart_pin: sb_can_th:PA10
tx_pin: sb_can_th:PA9
interpolate: false
run_current: 0.5
sense_resistor: 0.110
stealthchop_threshold: 0
##diag_pin: sb_can_th:PB5

[adxl345]
cs_pin: sb_can_th:PB12
spi_software_sclk_pin: sb_can_th:PB13
spi_software_mosi_pin: sb_can_th:PB15
spi_software_miso_pin: sb_can_th:PB14
axes_map: -y,z,-x

[resonance_tester]
accel_chip: adxl345
probe_points:
    100,100,20 # an example
	
# You will need to configure a neopixel (or other addressable led, such as dotstar). See
# https://www.klipper3d.org/Config_Reference.html#neopixel for configuration details.
# And you can get sb led MACRO here: https://github.com/PrinterConfigs/DoomConfig/blob/master/stealthburner.cfg
# Or here https://github.com/sttts/voron-klipper-config/blob/master/stealthburner_leds.cfg
[neopixel sb_leds]
pin: sb_can_th:PB1
chain_count: 3
color_order: GRBW
initial_RED: 0.5
initial_GREEN: 0.5
initial_BLUE: 0.5
initial_WHITE: 0.5

[fan]
pin: sb_can_th:PA2

[heater_fan hotend_fan]
pin: sb_can_th:PA3
shutdown_speed: 0

[output_pin activity_led]
pin: sb_can_th:PA1

# IO.0
# sb_can_th:PB6
# IO.1
# sb_can_th:PB11
# IO.2
# sb_can_th:PB7

#####################################################################
#       Probe
#####################################################################

[probe]
##      Inductive Probe - If you use this section , please comment the [bltouch] section
##      This probe is not used for Z height, only Quad Gantry Leveling
##      In Z+ position
##      If your probe is NO instead of NC, add change pin to ^sb_can_th:PB6
pin: sb_can_th:PB6 # In IN.0 position
x_offset: 0
y_offset: 25.0
z_offset: 0
speed: 10.0
samples: 3
samples_result: median
sample_retract_dist: 3.0
samples_tolerance: 0.006
samples_tolerance_retries: 3

#####################################################################
#       Bltouch
#####################################################################

#[bltouch]
##      Bltouch - If you use this section , please comment the [probe] section
##      More infomation at : https://www.klipper3d.org/BLTouch.html
##      This bltouch is not used for Z height, only Quad Gantry Leveling
##      In IO.1 position
#sensor_pin: sb_can_th:PB11 
##      In IO.2 Position
#control_pin: sb_can_th:PB7
#x_offset: 0
#y_offset: 25.0
#z_offset: 0
#speed: 10.0
#samples: 3
#samples_result: median
#sample_retract_dist: 3.0
#samples_tolerance: 0.006
#samples_tolerance_retries: 3

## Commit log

2022-11-19 Upload STLs and Klipper configuration file
    [Clockwork2.STL, main_body^Clockwork2(2)_Clockwork2.STL, motor_plate^Clockwork2(2)_Clockwork2.STL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]
2023-01-13 Fixed bottom layer
    Reoriented the model to print flat.
    Also, the added cable clip was 0.4mm below the rest of the part in Cura 5.2.1. I imported the model to Tinkercad and exported, this now works in Cura.
    Also, it appears this is the only modded part. The other files in this folder are Voron stock.
    [Clockwork2-adjusted.STL]
2023-01-13 Update README.md
    Note about fixed-up cable cover STL.
